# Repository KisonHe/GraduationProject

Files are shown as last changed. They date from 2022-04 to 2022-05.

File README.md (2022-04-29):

# ESP32 & RoboMaster motors
水毕设，3508+ESP_Dash，ESP32控制

## LVGL Note
注意检查style的生命周期，要与被赋予style的对象共存亡

```bash
node ./node_modules/lv_font_conv/lv_font_conv.js --font ~/Downloads/NotoSansMonoCJKsc-Regular.otf --symbol "123456abcdef我是中国人" --lcd --size 16 --bpp 4 --format bin -o data/customfont.bin
./node_modules/lv_img_conv/lv_img_conv.js ~/Downloads/gyro-200.png -f -c CF_TRUE_COLOR_ALPHA -t bin --binary-format 565 -o gyro.bin
```

获取Fonts `https://github.com/googlefonts/noto-cjk`

[Download](https://github.com/googlefonts/noto-cjk/raw/main/Sans/Mono/NotoSansMonoCJKsc-Regular.otf)

有空的时候记得修改 `https://github.com/KisonHe/TFT_eSPI_Assi` ，改成支持lv_font_conv

Get Offline Tool
```bash
npm i lv_font_conv
npm i lv_img_conv
```

## ESP32 Note
根据 https://github.com/espressif/arduino-esp32/issues/3079#issuecomment-520161166 
nnd,又要改，直接来吧！

## ESP32 - FreeRTOS
在Commit 754485b中，会出现manager或can read太久没有被执行的问题。TODO:目前没有完全理清楚，初步认定是TaskSkip导致的问题
https://docs.espressif.com/projects/esp-idf/en/v4.3.2/esp32/api-guides/freertos-smp.html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

有趣的现象，如果把lvgl的优先级从2改到22,反而不会出现电机疯掉问题了。初步认为wifi task，isr等以及一大堆task彻底抢占了core0,使得剩下的都在core1上，使得taskskip不再出现

一定要搞清楚！目前为了先弄毕业设计先都pin to core 1

排除以上问题，原因是can的接收频率不稳定，如果can rx是tskNO_AFFINITY则会出现接收频率降低问题。注意官方V4的example
```
xTaskCreatePinnedToCore(twai_receive_task, "TWAI_rx", 4096, NULL, RX_TASK_PRIO, NULL, tskNO_AFFINITY);
```
其中RX_TASK_PRIO为9,需要搞清楚为什么

目前在canrx处于tskNO_AFFINITY情况下，即使将lvgl task降到0也会导致canrx频率下降，急需弄清楚

似乎是因为偷懒带来的惨痛教训，从网上抄的CAN初始化没有仔细看，换成CAN_MODE_NORMAL后似乎没问题了。那么，nnd,为什么从2改到22,反而不会出现电机疯掉问题了？

Nope, is it caused by mqtt? Too late now debug tomorrow. Comment out MQTT see if problem still there. If caused by mqtt consider use https://docs.espressif.com/projects/esp-idf/en/latest/esp32/api-reference/protocols/mqtt.html

大概是WiFi Task在环境太糟糕的时候。。。大概会block太久？没验证，查看丢包现象观察猜测

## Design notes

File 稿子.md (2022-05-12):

1. 老师们好。我的题目是基于ESP32的物流节点设计。（看看别人怎么说的）（老师们辛苦了？）
2. 我的PPT内容主要分为选题背景与意义，主要工作内容，不足与展望和总结致谢。
3. 首先介绍选题背景与意义
4. 国务院发布的《国务院办公厅关于进一步推进物流降本增效 促进实体经济发展的意见》中有要求大力推进物联网等信息技术在物流服务中的应用。目前我国许多的物流控制系统仍然是有线方案。有线控制有很多不便，如扩展和结构调整麻烦等。
5. 目前，已经有人提出了基于ZigBee的无线方案，但Zigbee也有自身缺陷，如Zigbee的16位地址最大容纳不到65535个节点，传输速率也低，存在改进空间。
6. 综合现状与背景调查，可以整理需求。一，需要实现无线组网，并且所选协议可靠简便，可扩展性高。二，组网完成后的通信协议能方便的与物流控制系统进行通信，回报电机数据，被物流系统控制。此外，作为物流控制节点，常常有传感器数据需要回报，因此节点需要可以回报给物流系统一些传感器的值。三，需要能够路程/速度闭环控制电机。四，人员能够方便的现场查看与调试电机、网络。
7. 接下来介绍主要工作内容
8. 由需求可以定义出系统的功能模块，分为图中的这些功能模块。
9. 由功能模块可以大致设计出系统的组成，分为图中的这些模块，软件开发上使用VSCode+Platformio平台开发，利用C++与设计模式，对软件进行优化，方便接入更多功能。
10. 总体结果上，实现了所有的需求点。完成PCB设计与制作，能够对电机进行路程/速度的闭环控制。现场人员能够通过触摸屏、手机网页对电机进行控制。为了验证被系统控制的可行性，自行编写了物流系统的模拟程序，可以读取电机的各种值，并对电机进行控制。并对嵌入式软件进行了多种优化，如Wi-Fi断联自动重建http与mqtt连接，中文显示启用超分辨率增加可读性，使用NVS存储触摸校准数据等等。
11. 本设计软件上留出了接口，可以方便的进行修改。ESP32支持多分区OTA更新，使得固件更新并不困难。
12. 现在简要介绍一下为什么选择ESP32。ESP32是我国乐鑫公司生产的，不仅在行业广泛使用，同时在各种创客社区也有大量使用的爆款单片机，拥有所示的多种强大优点，对比其他同类产品开发简单，价格低廉，性能强劲。
13. M3508减速电机套是深圳大疆公司研制的一款电机。配备大疆创新公司定制的FOC电调，可以广泛应用于机器人移动平台动力、驱动模块等机构中。M3508电机配套的C620电调可以使用CAN总线进行控制，CAN总线非常稳定，这种控制方式也让控制多个电机不成问题。满足本设计的要求，极大的简化了MCU端的电路与软件设计，非常适合本设计。由于软件有充分的解偶性，使用C++开发。如果用户希望更换电机，仅需更换极少的驱动代码即可。
14. 这是PCB硬件的原理图
15. 以及布线和PCB实物
16. MQTT是物联网行业广泛使用的一种通信协议。MQTT使用订阅发布机制，因此需要中心通信节点。为了方便使用，在阿里云上搭建了MQTT中转服务器。
17. 首先演示触摸屏。开发人员可以使用触摸屏查看各种信息。先来看网络部分，可以显示信号强度，IP地址，连接的AP的名字与BSSID,对网络查找问题很有帮助。还可以查看通过板上预留的SPI、串口、I2C等接口连接的传感器值。可以控制电机，这里设置转速为1500,可以看到信息界面显示了运行态为速度闭环。还可以设置为路程闭环，这里设置目标路程为320,可以看到电机迅速转到目标位置并停下。设置路程为3320度，可以看到用手去迫使电机偏移，电机会自动回到设定的的位置。现场人员的安全最重要，一旦设定为安全模式，会无视任何指令，将电机的扭矩设置为零。
18. 接下来演示模拟物流控制系统。首先登陆到物流控制系统，模拟物流控制系统的主界面，支持命令自动补全。最下面一栏显示了被控制的节点ID,对应的详细信息，包括转速、路程、PID参数、传感器信息等。接下来设置转速为 1000,可以看到电机开始起转，并且屏幕正确显示了对应的信息。然后演示设置不同的速度。接下来演示设置路程闭环，设置 路程 为 3000,可以看到电机改为路程闭环运行，并且迅速的到达目标位置。演示设置 路程 为 0。接下来设置一个远一点的路程 为 -10000，可以看到电机以最高速度快速到达目标位置。还可以设置PID参数，设置外环 kP 为 0.2，可以在嵌入式屏幕以及最下栏看到更新，设置内环 kP 为 20，可以在嵌入式屏幕看到更新，最下栏显示空间不足未显示，设置内环 kI 为 0.2，可以在嵌入式屏幕看到更新，设置外环 kP 为 0.1，最后退出模拟物流控制系统
19. 接下来演示手机控制界面，连接到网页后，现场人员可以查看一些系统基本信息。可以选择不同的控制方式，可以看到嵌入式屏幕有所更新。接下来设置速度，可以看到电机起转，屏幕有所更新。设置不同的转速。接下来演示路程控制，可以看到电机改为路程闭环运行，并且迅速的到达目标位置。还可以改变内环PID参数的值，可以看到屏幕有所更新。
20. HTTP的代码体积较大，尝试精简之后仍有627k,尽管ESP32有16MB的Flash空间，但节约一些总是好的。因此，将网页放在SPIFFS中而不是代码段中。这样OTA软件便可以精简体积。同时使用gzip对网页进行压缩，进一步减少网页文件体积。可以看到压缩后的文件大小仅为源文件的24%。
21. 电阻式触摸屏需要校准，不同的屏幕校准值不同。校准值写死在程序段中会导致量产不便。因此，使用NVS存储，自动判断是否需要校准，接下来演示该过程。利用串口日志揭示系统中发生了什么。
22. 全新的单片机启动后，会发现NVS存储中没有校准数据，开始校准过程。校准完成后，系统会启动。这里我们复位一下ESP32，可以看到启动完成了校准数据的读取。
23. 为了效果更好的显示中文，使用抗锯齿与亚像素渲染。现代的个人设备几乎没有不使用这两个技术的，但是嵌入式设备上普及率不高。抗锯齿就是利用灰度营造平滑的感觉，亚像素就是利用屏幕的像素排列减少锯齿感。
24. 工业环境要求高，因此WiFi连接丢失后必须尽快重连并且重新建立MQTT的控制连接。这里通过拔掉路由器电源模拟Wi-Fi丢失，可以看到插上电源后自动重连。
25. 由于时间以及个人能力有限，在本设计中还有很多可以改进的地方。可以换用ESP32-S3。ESP32的勘误表中有许多关于CAN的硬件问题，有的可以通过软件规避，有的不可以。ESP32S3是乐鑫最新的单片机之一，修正了大量ESP32的问题，可以外带更多Flash,更多PSRAM,甚至片内集成了JTag调试器，无需额外购买调试设备。是行业的领先方案。还应该留出PCB的固定孔，方便PCB的固定。还可以换电容屏，触摸更精确，体验更好。
26. 感谢各位老师的聆听，还请各位老师批评指正

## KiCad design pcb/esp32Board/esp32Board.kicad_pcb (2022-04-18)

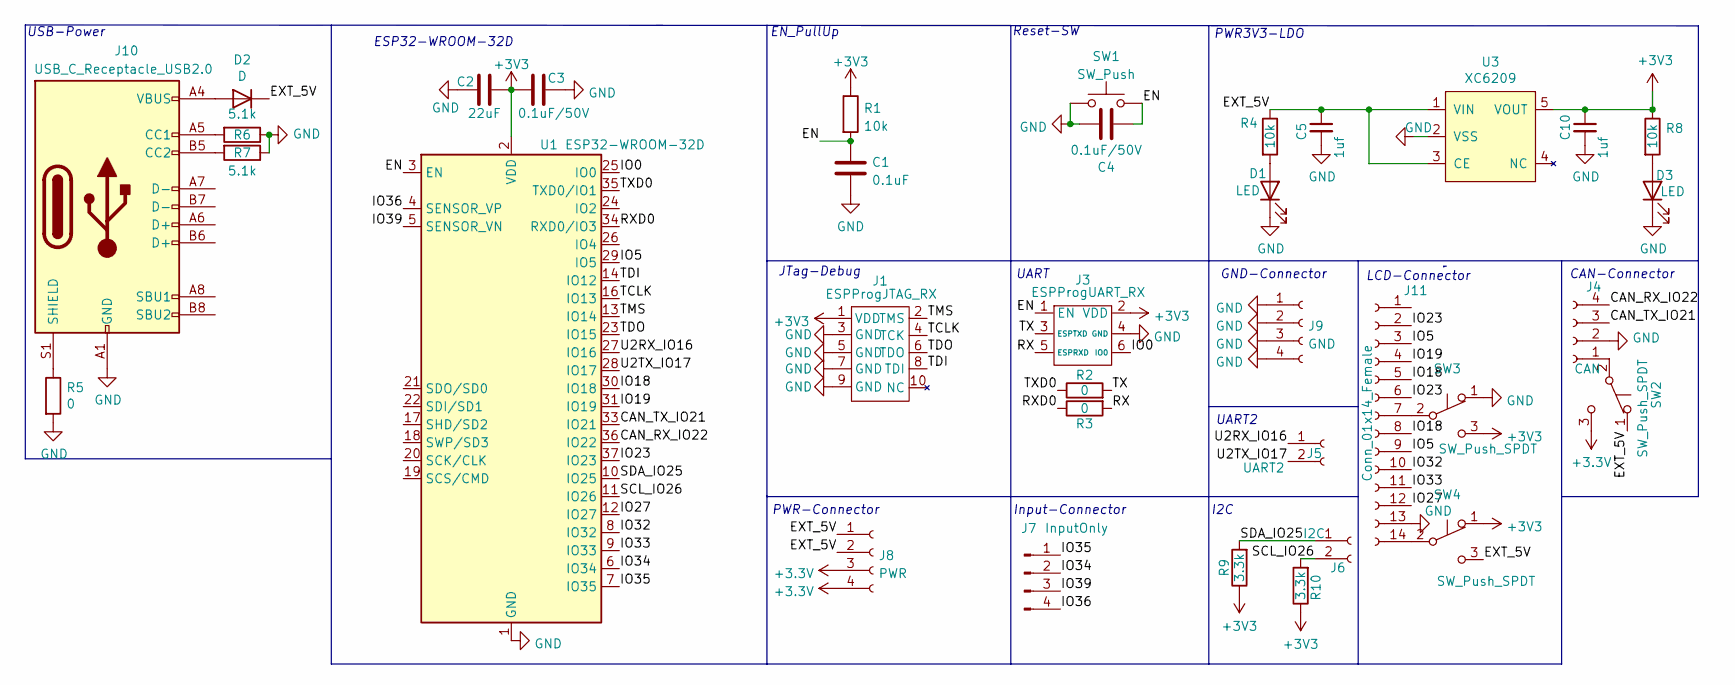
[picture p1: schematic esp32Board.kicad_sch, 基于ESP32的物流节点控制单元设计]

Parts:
C1: 0.1uF; C_0603_1608Metric; LCSC C1591
C2: 22uF; C_0603_1608Metric
C3, C4: 0.1uF/50V; C_0603_1608Metric
C5, C10: 1uf; C_0603_1608Metric
D1, D3: LED; LED_0603_1608Metric; LCSC C181863
D2: D; C8678; LCSC C8678
J1: ESPProgJTAG_RX; IDC_1.27mm_10P
J3: ESPProgUART_RX; IDC_1.27mm_6P
J4: CAN; PinHeader_1x04_P2.54mm_Vertical
J5: UART2; PinHeader_1x02_P2.54mm_Vertical
J6: I2C; PinHeader_1x02_P2.54mm_Vertical
J7: InputOnly; PinHeader_1x04_P2.54mm_Vertical
J8: PWR; PinHeader_1x04_P2.54mm_Vertical
J9: GND; PinHeader_1x04_P2.54mm_Vertical
J10: USB_C_Receptacle_USB2.0; USB_C_Receptacle_HRO_TYPE-C-31-M-12; LCSC C165948
J11: Conn_01x14_Female; PinHeader_1x14_P2.54mm_Vertical
R1, R4, R8: 10k; R_0603_1608Metric
R2, R3, R5: 0; R_0603_1608Metric; LCSC C429617
R6, R7: 5.1k; R_0603_1608Metric; LCSC C325524
R9, R10: 3.3k; R_0603_1608Metric; LCSC C429617
SW1: SW_Push; BTN-TS342A4P-WZ-C557592; LCSC C557592
SW2, SW3, SW4: SW_Push_SPDT; 0603JumperP3
U1: ESP32-WROOM-32D; ESP32-WROOM-32
U3: XC6209; SOT-23-5

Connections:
/CAN_RX_IO22: J4.4, U1.36 (IO22)
/CAN_TX_IO21: J4.3, U1.33 (IO21)
/EN: C1.1, C4.1, J3.1 (EN), R1.2, SW1.2, U1.3 (EN)
/EXT_5V: C5.1, D2.1 (K), J8.1, J8.2, R4.1, SW2.1 (A), SW4.3 (C), U3.1 (VIN), U3.3 (CE)
/IO0: J3.6 (IO0), U1.25 (IO0)
/IO5: J11.3, J11.9, U1.29 (IO5)
/IO18: J11.5, J11.8, U1.30 (IO18)
/IO19: J11.4, U1.31 (IO19)
/IO23: J11.2, J11.6, U1.37 (IO23)
/IO27: J11.12, U1.12 (IO27)
/IO32: J11.10, U1.8 (IO32)
/IO33: J11.11, U1.9 (IO33)
/IO34: J7.2, U1.6 (IO34)
/IO35: J7.1, U1.7 (IO35)
/IO36: J7.4, U1.4 (SENSOR_VP)
/IO39: J7.3, U1.5 (SENSOR_VN)
/RX: J3.5 (ESPRXD), R3.2
/RXD0: R3.1, U1.34 (RXD0/IO3)
/SCL_IO26: J6.2, R10.2, U1.11 (IO26)
/SDA_IO25: J6.1, R9.2, U1.10 (IO25)
/TCLK: J1.4 (TCK), U1.16 (IO13)
/TDI: J1.8 (TDI), U1.14 (IO12)
/TDO: J1.6 (TDO), U1.23 (IO15)
/TMS: J1.2 (TMS), U1.13 (IO14)
/TX: J3.3 (ESPTXD), R2.2
/TXD0: R2.1, U1.35 (TXD0/IO1)
/U2RX_IO16: J5.1, U1.27 (IO16)
/U2TX_IO17: J5.2, U1.28 (IO17)
GND: C1.2, C2.1, C3.2, C4.2, C5.2, C10.2, D1.1 (K), D3.1 (K), J1.3 (GND), J1.5 (GND), J1.7 (GND), J1.9 (GND), J3.4 (GND), J4.2, J9.1, J9.2, J9.3, J9.4, J10.A1 (GND), J10.A12 (GND), J10.B1 (GND), J10.B12 (GND), J11.13, R5.2, R6.1, R7.1, SW1.1, SW3.1 (A), U1.1 (GND), U1.15 (GND), U1.38 (GND), U1.39 (GND), U3.2 (VSS)
unnamed: D1.2 (A), R4.2
unnamed: D2.2 (A), J10.A4 (VBUS), J10.A9 (VBUS), J10.B4 (VBUS), J10.B9 (VBUS)
unnamed: D3.2 (A), R8.2
unnamed: J4.1, SW2.2 (B)
unnamed: J10.A5 (CC1), R6.2
unnamed: J10.B5 (CC2), R7.2
unnamed: J10.S1 (SHIELD), R5.1
unnamed: J11.7, SW3.2 (B)
unnamed: J11.14, SW4.2 (B)

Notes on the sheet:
ESP32-WROOM-32D
Input-Connector
LCD-Connector
PWR3V3-LDO
CAN-Connector
USB-Power
EN_PullUp
UART
I2C
GND-Connector
JTag-Debug
Reset-SW
UART2
PWR-Connector

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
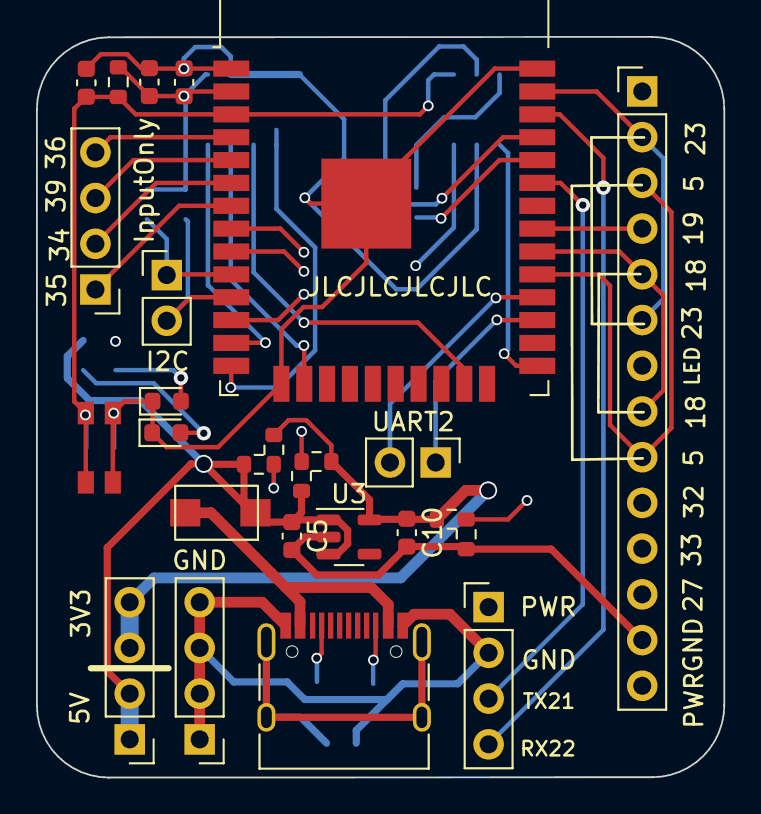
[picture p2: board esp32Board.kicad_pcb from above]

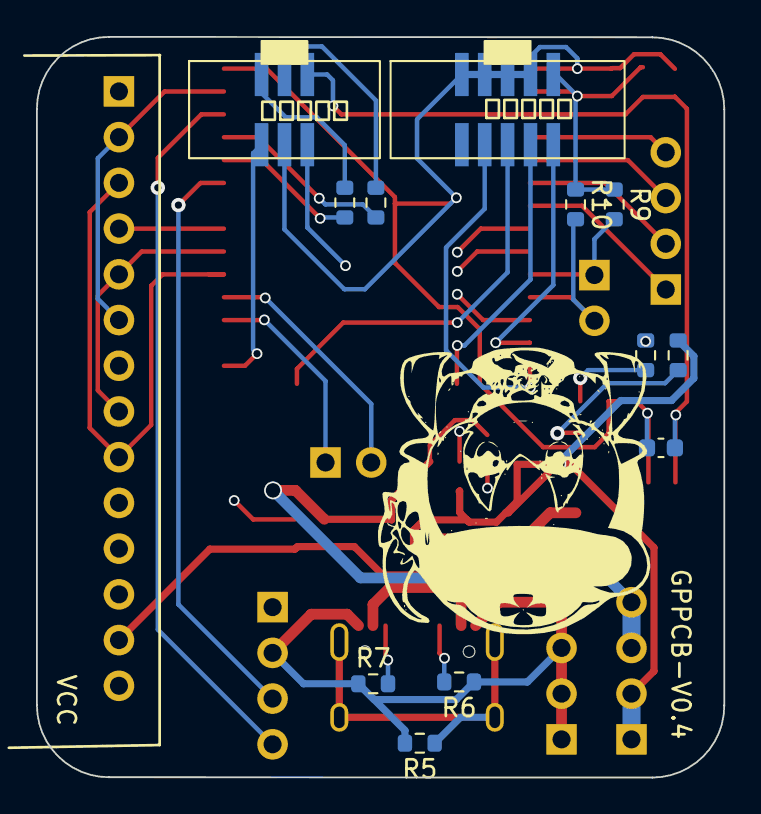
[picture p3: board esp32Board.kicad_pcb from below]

Board: 4 copper layers, 38.2 x 41.1 mm, 35 parts (12 on the bottom side), 39 nets.

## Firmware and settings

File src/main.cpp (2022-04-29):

#include <Arduino.h>

#include <WiFi.h>
#include <AsyncTCP.h>
#include <ESPAsyncWebServer.h>

#include <ESPDash.h>

#include "mqtt.h"

#include "pidCardSet.h"
#include "motorCardSet.h"

#include "can.h"
#include "rm_can_motors.h"
#include <lvgl.h>
#include <TFT_eSPI.h>
#include "SPIFFS.h"
#include "nvs_flash.h"
#include "nvs.h"
#include <stdio.h>

#include "gui/gui.h"

const char *ssid = "btw_i_use_arch";    // SSID
const char *password = "azxcvbnm"; // Password
extern int16_t output;
extern int16_t rxhz;
extern int16_t txhz;
extern canMotors::motor M3508;
// char cpuStatus[200];
nvs_handle nvs_main_handle;

/* Start Webserver */
AsyncWebServer server(80);

/* Attach ESP-DASH to AsyncWebServer */
ESPDash dashboard(&server);

pid motorPID(1, 0, 0, 0, 100);
pidCardSet inPIDSet(&dashboard, M3508.getInPID());
motorCardSet mainMotorSet(&dashboard, &M3508);
unsigned long manager_exe_time = 0;
extern SemaphoreHandle_t stopMQTTTask;
void WiFiStationDisconnected(WiFiEvent_t event, WiFiEventInfo_t info){
    log_e("Disconnected from WiFi access point\nWiFi lost connection. Reason: %d\nTrying to Reconnect",info.disconnected.reason);
    WiFi.begin(ssid, password);
    stopMQTT();
    server.end();
}

void WiFiStationConnected(WiFiEvent_t event, WiFiEventInfo_t info){
    log_w("Connected to AP successfully!");
}

void WiFiGotIP(WiFiEvent_t event, WiFiEventInfo_t info){
    log_w("Got IP address: %s",WiFi.localIP().toString().c_str());
    startMQTT();
    server.begin();
}

void setup()
{
    stopMQTTTask = xSemaphoreCreateMutex();
    Serial.begin(115200); /* prepare for possible serial debug */
    Serial.println();
    SPIFFS.begin();
    esp_err_t err = nvs_flash_init();
    if (err == ESP_ERR_NVS_NO_FREE_PAGES || err == ESP_ERR_NVS_NEW_VERSION_FOUND)
    {
        // NVS partition was truncated and needs to be erased
        // Retry nvs_flash_init
        log_w("NVS partition was truncated and needs to be erased,erasing now");
        ESP_ERROR_CHECK(nvs_flash_erase());
        err = nvs_flash_init();
    }
    err = nvs_open("storage", NVS_READWRITE, &nvs_main_handle);
    if (err != ESP_OK){
        log_e("Unexpected Error at nvs_open:%s",esp_err_to_name(err));
    }

    if (can_init() != ESP_OK){
        log_e("CAN init failed!");
    }
    motorPID.attach(inPIDSet);
    guiSetUp();
    /* Connect WiFi */
    WiFi.mode(WIFI_STA);
    WiFi.onEvent(WiFiGotIP, SYSTEM_EVENT_STA_GOT_IP);
    WiFi.onEvent(WiFiStationConnected, SYSTEM_EVENT_STA_CONNECTED);
    WiFi.onEvent(WiFiStationDisconnected, SYSTEM_EVENT_STA_DISCONNECTED);
    WiFi.begin(ssid, password);
    vTaskDelay(1000);
    
}
// extern int32_t mark;
void loop()
{
    // static int cnt=0;
    // cnt++;
    if (WiFi.isConnected()){
        mainMotorSet.update();
        dashboard.sendUpdates(); // Dont send too fast or get "ERROR: Too many messages queued". 10Hz is more than surely enough
    }
    // if (cnt>3||(rxhz<900||txhz<900)){
    //     cnt=0;
    //     log_w("RXHz = %d, TXHz = %d, manager run spent %ld",rxhz,txhz,manager_exe_time);
    //     can_status_info_t tmp_info;
    //     can_get_status_info(&tmp_info);
    //     log_w("state:%d msgs_to_tx:%d msgs_to_rx:%d rx_missed_count:%d bus_error_count:%d tx_error_counter:%d rx_error_counter:%d",\
    //     tmp_info.state,tmp_info.msgs_to_tx,tmp_info.msgs_to_rx,tmp_info.rx_missed_count,tmp_info.bus_error_count,tmp_info.bus_error_count,tmp_info.tx_error_counter,tmp_info.rx_error_counter);
    //     // rxhz = 0;txhz = 0;
    // }
        
    vTaskDelay(300);
}

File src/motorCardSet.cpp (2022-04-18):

#include "motorCardSet.h"
#include <functional>

extern bool ignoreCMD;
extern bool setSafe;
extern canMotors::motor M3508;

motorCardSet::motorCardSet(ESPDash* dashboard, canMotors::motor* motor):dashboard(dashboard),motorInstance(motor)
{
    distanceControl = new Card(dashboard, BUTTON_CARD, "路程控制");
    rpm = new Card(dashboard, SLIDER_CARD, "转速","RPM",-6000,6000);
    distance = new Card(dashboard, SLIDER_CARD, "路程","角度",-18000,18000);
    
    distanceControl->attachCallback([this](bool value){
        if ((!ignoreCMD)&&(!setSafe)){
            if (value){// spd to pos control
                this->motorInstance->Angle_Set(this->motorInstance->GetSoftAngle());//设置当前值为目标值防止乱转
                this->distance->update(this->motorInstance->GetSoftAngle());
                this->isPosCtl = true;
            }else{   // pos to spd control
                this->motorInstance->Speed_Set(0);
                this->rpm->update(0);
                this->isPosCtl = false;
            }
        }
        this->distanceControl->update(value);
    });
    // distanceControl->attachCallback(distanceControlcbf);
    rpm->attachCallback([this](int value){
        this->rpm->update(value);// 本来应该放在if (!this->isPosCtl)里面决定是否update
                                //如果不符合应该拒绝更新，但是espdash的逻辑会认定这个没有更新导致网页hang在错误的位置
                                //所以无条件update
        if (!this->isPosCtl){
            if ((!ignoreCMD)&&(!setSafe)){
                this->motorInstance->Speed_Set(value);
            }
        }
    });
    distance->attachCallback([this](int value){
        this->distance->update(value);
        if (this->isPosCtl){
            if ((!ignoreCMD)&&(!setSafe)){
                this->motorInstance->Angle_Set(value);
            }
        }
    });
    
}

void motorCardSet::update(){
    isPosCtl = M3508.RunState == canMotors::RunState_t::Speed_Ctl ? false : 
                                                                    M3508.RunState == canMotors::RunState_t::Position_Ctl ? true : isPosCtl;
    distanceControl->update(isPosCtl);
    if (isPosCtl){
        rpm->update(motorInstance->GetRealSpeed());
        distance->update(motorInstance->GetTargetSoftAngle());
    }else{
        distance->update(motorInstance->GetSoftAngle());
        rpm->update(motorInstance->GetTargetSpeed());
    }
    
    
}


motorCardSet::~motorCardSet()
{
}

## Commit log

2022-03-19 PIDCardSet V1
    [partitions_custom.csv]
2022-03-22 PCB Update
    [esp32Board.kicad_pcb, esp32Board.kicad_sch]
2022-03-22 can motors
2022-03-26 Fix PCB Error
    [esp32Board.kicad_pcb]
2022-03-26 PID区间I积分
2022-03-26 使用新的PCB
2022-03-27 Add partition
    [partitions_custom16M.csv]
2022-03-27 更新描述
2022-03-27 modify esp-dash source code
    Because the button is on top of card button,
    preventing people from pressing the card button
2022-03-27 Update ini
    esp-dash is using ArduinoJson already
2022-03-28 PCB V0.2
    [esp32Board.kicad_pcb, esp32Board.kicad_sch]
2022-03-28 Bug Fix PID hang
2022-03-29 制作代码垃圾
2022-04-08 Add motor tab label
2022-04-12 Add FrameWork
2022-04-12 Put ESP-Dash's web into spiffs
    [partitions_custom.csv]
2022-04-12 Fix rpmMeter SCROLLABLE bug
    [lv_motor_tab.cpp]
2022-04-13 Use XC6209 instead of trash XC6206
    [esp32Board.kicad_pcb, esp32Board.kicad_sch]
2022-04-14 Fix I2C Pull Up
    https://github.com/espressif/arduino-esp32/issues/3424 Damn why not design it strong enough so bad
    [esp32Board.kicad_pcb, esp32Board.kicad_sch]
2022-04-14 Switch to more stable aliyun mqtt broker
    [mqtt.cpp]
2022-04-18 Update sch with blocks
    [esp32Board.kicad_sch]
2022-04-18 Fix CAN Bus Bug
    [gui.cpp, main.cpp]
2022-04-18 Update PCB
    [esp32Board.kicad_pcb]
2022-04-23 Add Calib button
2022-04-29 Fix CAN lose frame problem
    [main.cpp, mqtt.cpp]
2022-05-11 改成竖的，论文好看
    [esp32Board.kicad_sch]
